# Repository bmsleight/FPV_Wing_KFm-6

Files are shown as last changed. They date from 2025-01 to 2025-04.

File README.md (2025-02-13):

# FPV_Wing_KFm-6

Simple FPV wing model based upon simply cut foam sheets and simple 3d parts

## Basic Materials

The naked model is less than £9. Wingspan 594mm (or 705mm including body).

Aim to have construction to be as simple as possible. So based all dimensions upon A4, 3mm deep foam board. Combined with some 3d printed parts.

Key: Yellow: foam board, Green: Printed parts

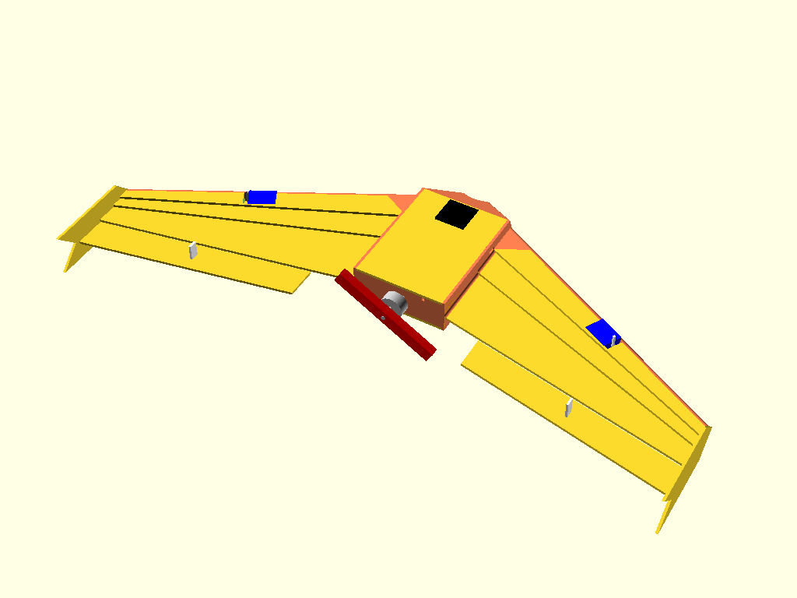
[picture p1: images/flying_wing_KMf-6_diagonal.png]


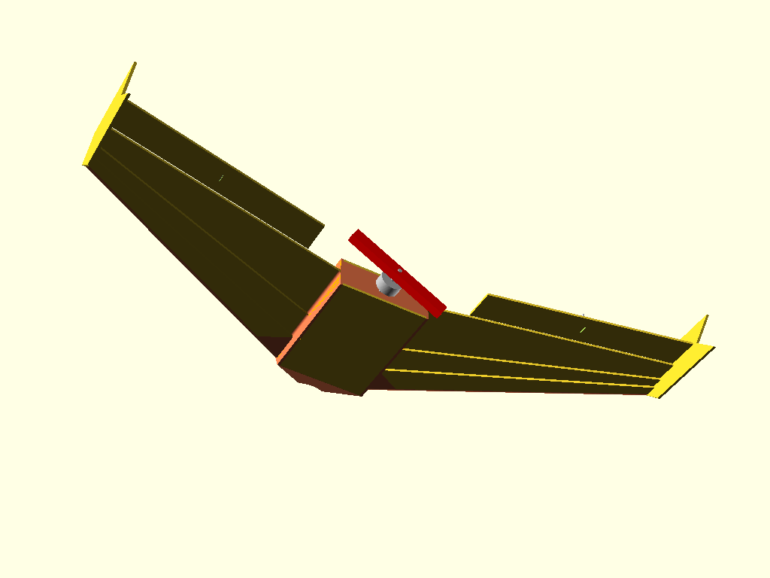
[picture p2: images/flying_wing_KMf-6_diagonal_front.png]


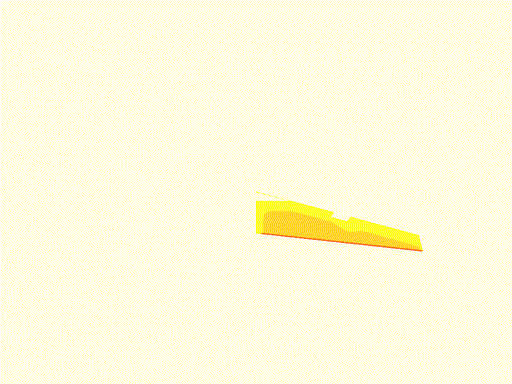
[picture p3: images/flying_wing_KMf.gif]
Model rotated


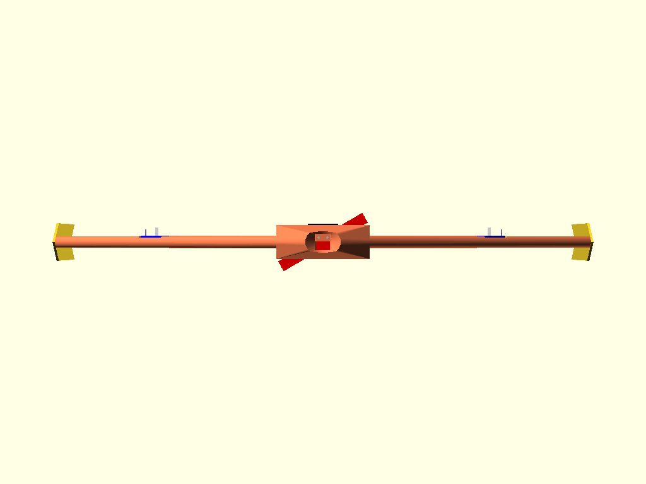
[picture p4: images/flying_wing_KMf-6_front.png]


[Center of Gravity at ~76mm back](http://rcwingcog.a0001.net/?i=1)

## FPV

Total cost, including motors, flight controller, analogue camera, battery, GPS is  £121.63 I was aiming for less than  £100.

## What Makes it Simple

The cuts use the most of the natural dimension of A4 sheets. 

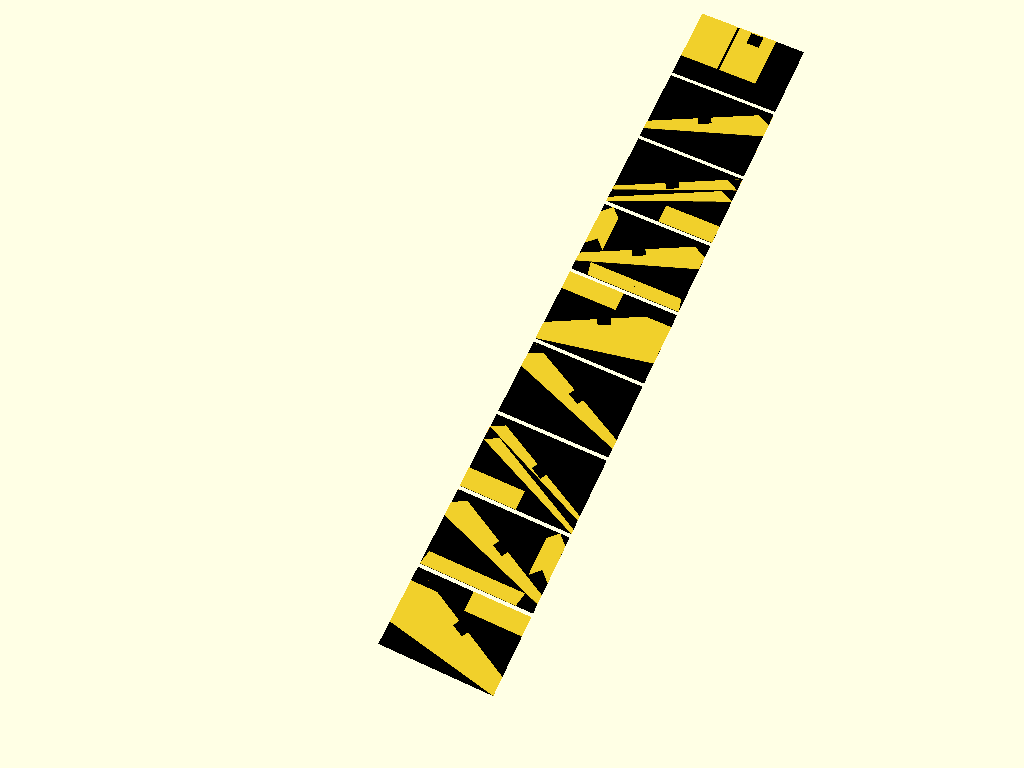
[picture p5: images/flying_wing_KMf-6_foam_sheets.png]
Sheets


Only eight sheets are needed. The model can export directly the SVG file, per page, for printing a template.

Model

The 3d parts can be printed on a standard 200x200 print bed, with only one part requiring supports. The seven individual parts in the [stl directory](https://github.com/bmsleight/FPV_Wing_KFm-6/tree/main/stl)

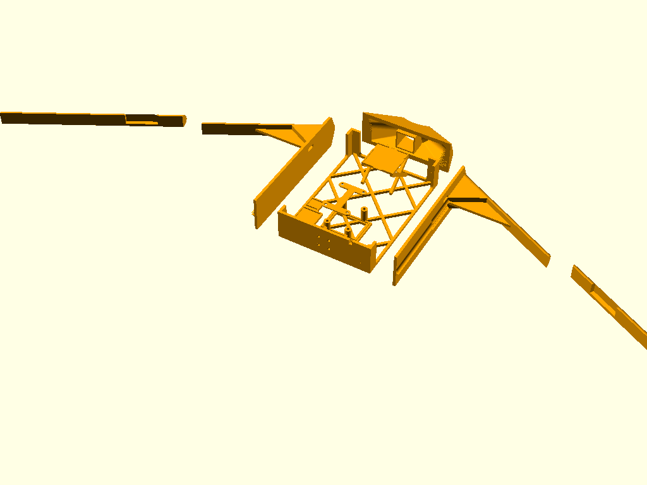
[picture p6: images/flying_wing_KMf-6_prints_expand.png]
https://github.com/bmsleight/FPV_Wing_KFm-6/tree/main/stl Prints Expanded


Model expanded rotated

## Model 

From within OpenSCAD.

Amend display variable to 1 - display model, 2 - print all the printed parts as a print bead, 3 - All the foam parts, 4 - All foam parts as SVGs, 5 - One page SVG file. 

```
display = 1;

module display(display=display)
{
    if(display==1)
    {
        display_model(foam=true, printed_part=true);
    }
    if(display==2)
    {
        print_all();
    }
    if(display==3)
    {
        print_foam_all(outline=true);
    }
    if(display==4)
    {
        projection() print_foam_all(outline=false);
    }
    if(display==5)
    {
        projection() print_foam(page=2, outline=false);
    }
}

display();
```

## Will it Fly ?

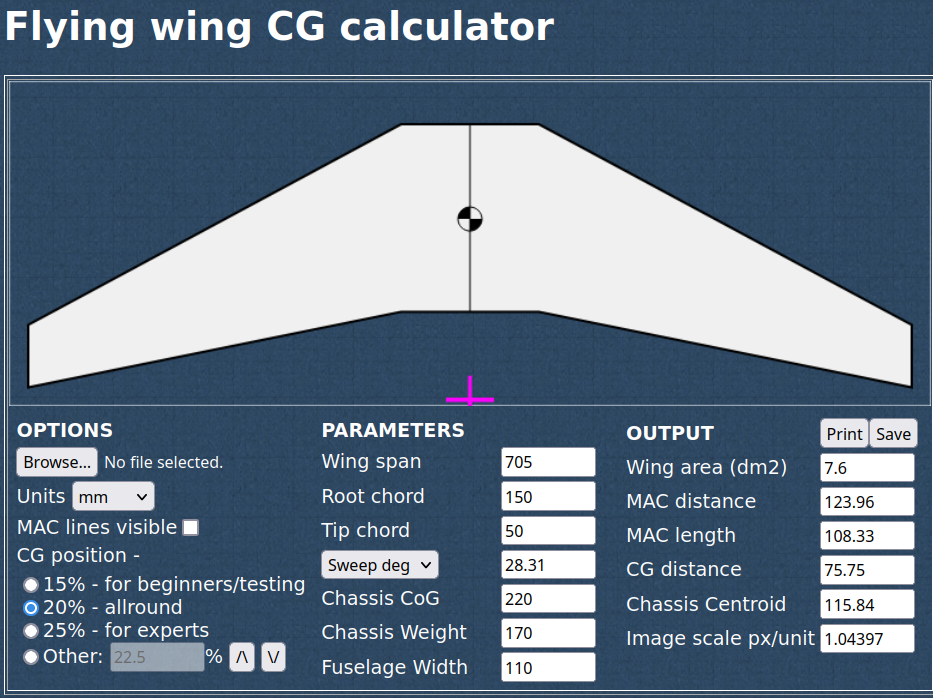
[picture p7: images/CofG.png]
C of G


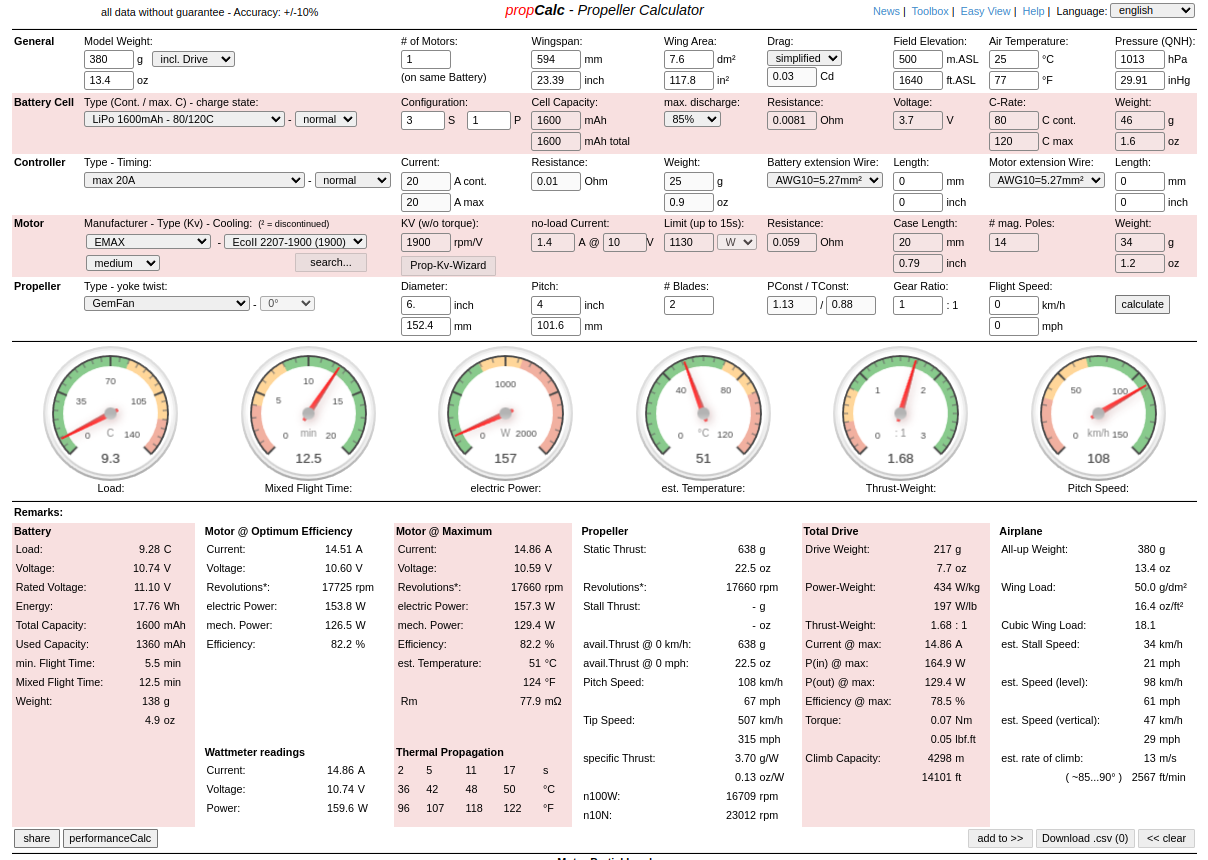
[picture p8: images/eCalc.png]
eCalc


## Parts 

* Printed parts single shell, 15% infill
* Foam board 3mm A4
* Total for naked wing, including glue: 162 grammes 
* ESC 40g  https://www.unmannedtechshop.co.uk/product/dys-20a-2-4s-brushless-esc-with-5v-2a-bec-for-rc-fixed-wing-aircraft/
* Motor 32g https://www.unmannedtechshop.co.uk/product/emax-eco-ii-series-2207-motor/
* Battery 70g, 4S 650mah
 Props https://www.unmannedtechshop.co.uk/product/hqprop-t5-1x2-5x3-grey-propeller-2cw2ccw/
* camera VTX  https://www.aliexpress.com/item/1005008234258917.html?spm=a2g0o.cart.0.0.5ac538dalBiVNT&mp=1 and generic Camera 
* Flight controller (5.6g) https://www.hobbyrc.co.uk/speedybee-f405-wing-mini-flight-controller
* https://www.unmannedtechshop.co.uk/product/tbs-m10-gps-glonass-module/
* servos
* Servo horns https://www.amazon.co.uk/gp/product/B08MDXD3C1/

## Photos

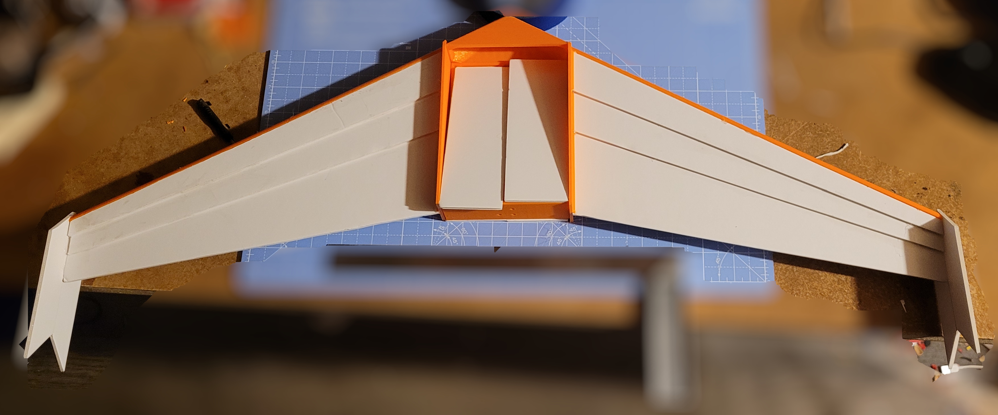
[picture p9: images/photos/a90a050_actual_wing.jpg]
Build naked model


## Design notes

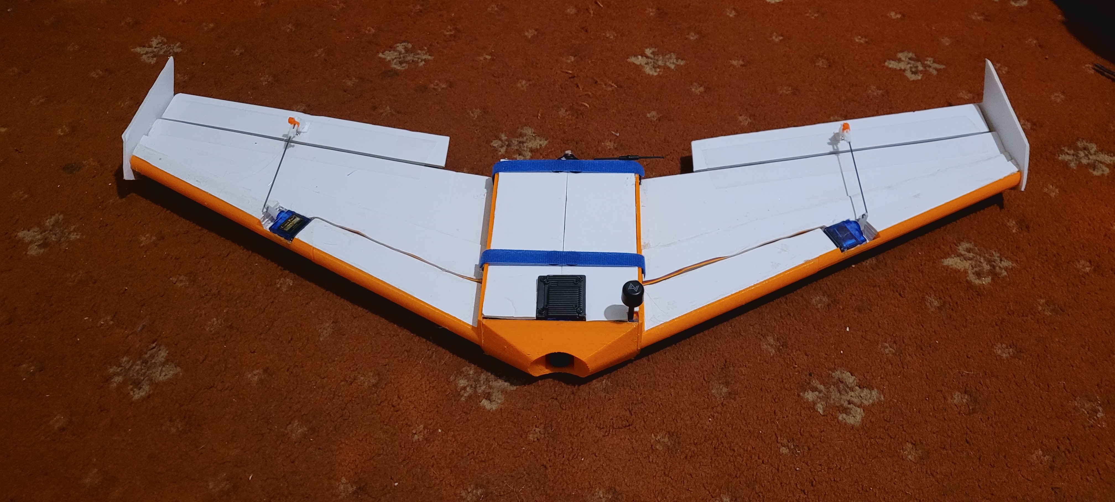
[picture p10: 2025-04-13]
images/photos/aa8055b_actual_wing.jpg

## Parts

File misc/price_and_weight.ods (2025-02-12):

 |  |  |  | £239 | 379.1 g
Frame – foam and prints | 1 | £9 | 161.0 g | £9 | 161.0 g
Batteries – (already had) | 1 | £16 | 100.0 g | £16 | 100.0 g
VTX | 1 | £159 | 22.6 g | £159 | 22.6 g
ESC | 1 | £8 | 40.0 g | £8 | 40.0 g
Motor | 1 | £13 | 31.5 g | £13 | 31.5 g
FC | 1 | £30 | 5.6 g | £30 | 5.6 g
Servo | 2 | £2 | 9.2 g | £4 | 18.4 g

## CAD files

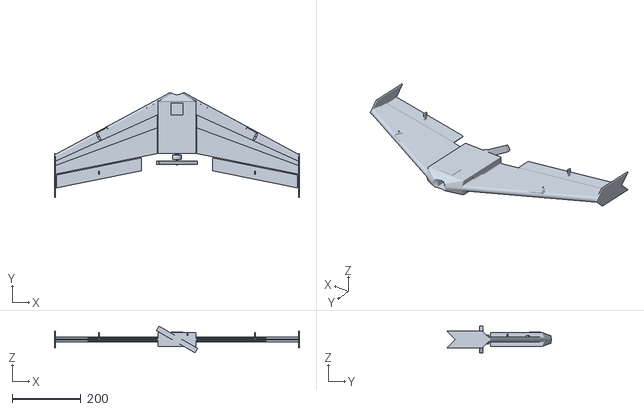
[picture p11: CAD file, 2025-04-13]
stl/flying_wing_KMf-6_full_model.stl
711.0 x 304.0 x 77.7

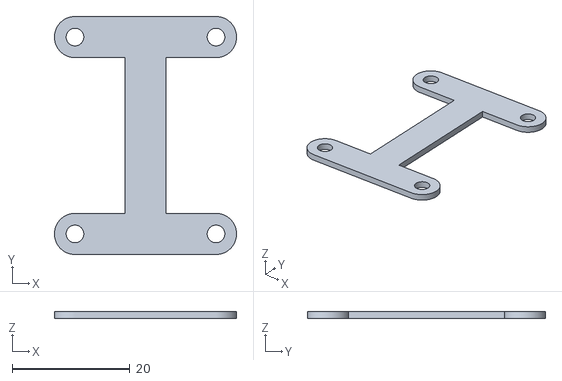
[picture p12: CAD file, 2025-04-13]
stl/flying_wing_KMf-6_printed_part_fc_lid.stl
31.0 x 40.5 x 1.25

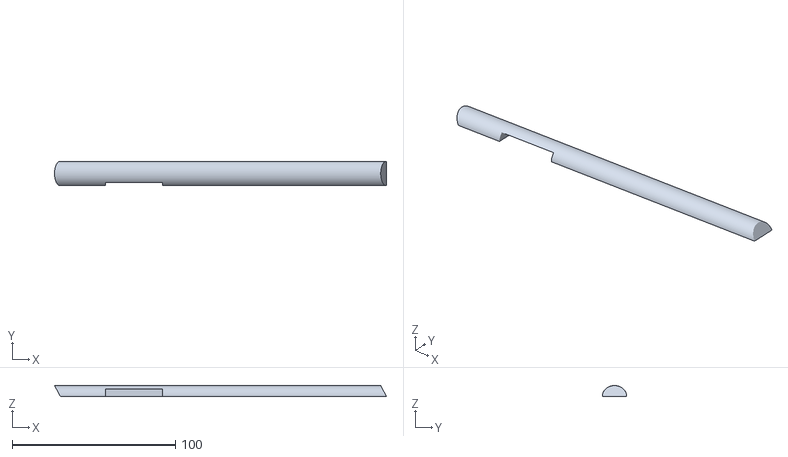
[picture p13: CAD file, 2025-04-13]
stl/flying_wing_KMf-6_printed_part_leading_edge_half.stl
203.5 x 15.0 x 6.71

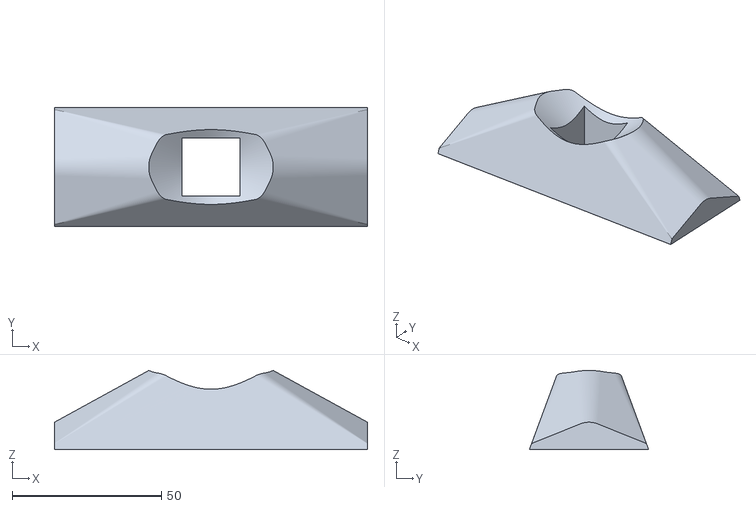
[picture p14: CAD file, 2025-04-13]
stl/flying_wing_KMf-6_printed_part_cockpit_front.stl
105.0 x 40.0 x 26.5

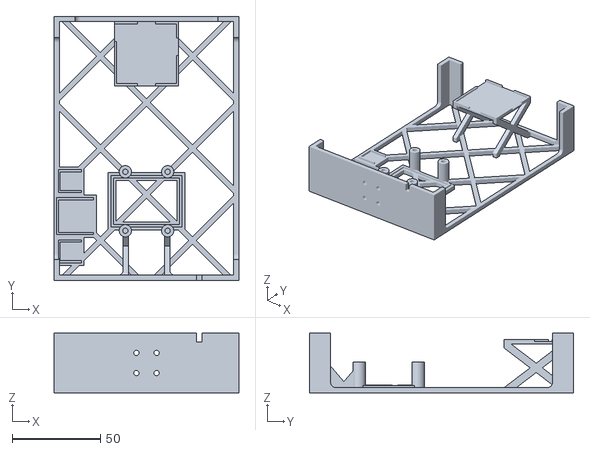
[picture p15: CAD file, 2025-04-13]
stl/flying_wing_KMf-6_printed_part_cockpit.stl
104.8 x 149.9 x 34.0

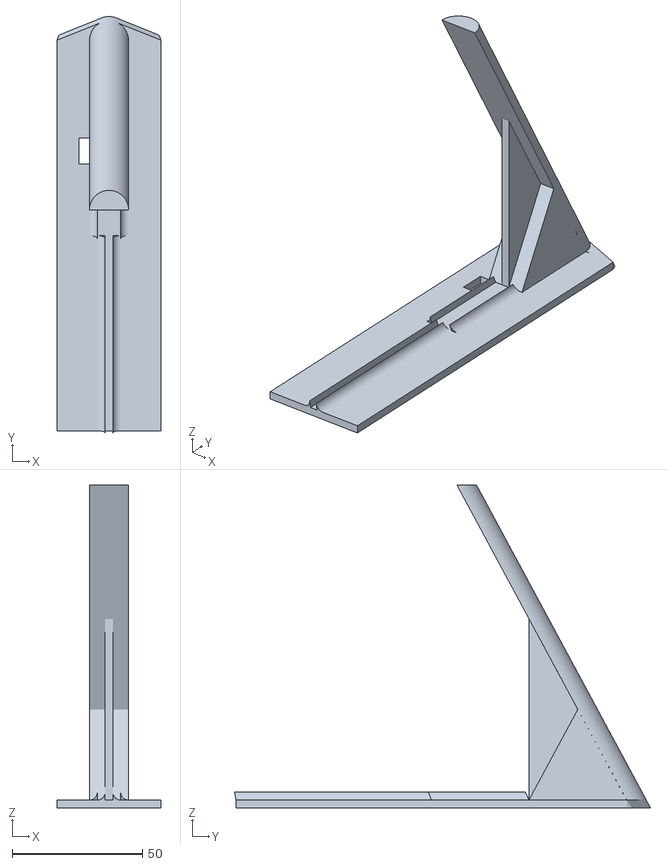
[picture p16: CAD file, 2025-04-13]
stl/flying_wing_KMf-6_printed_part_side_panel.stl
40.0 x 159.8 x 123.9

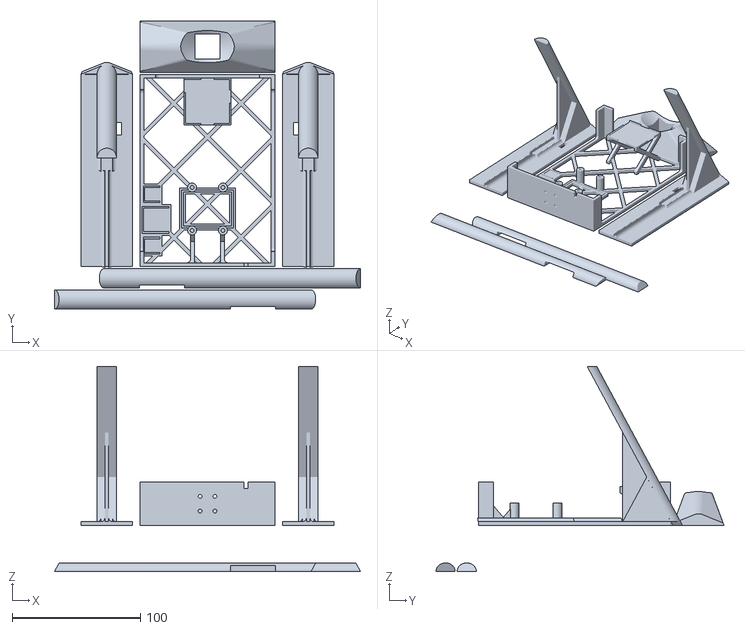
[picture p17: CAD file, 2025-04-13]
stl/flying_wing_KMf-6_printed_parts.stl
238.4 x 224.5 x 159.7

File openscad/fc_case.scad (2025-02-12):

$fn=60;

module pillar(od=7,id=3,ox, oy, oz)
{
    translate([ox/2,oy+od/2,0]) difference()
    {
        cylinder(h=oz,d=od,center=true);
        translate([0,0,oz]) cylinder(h=oz*2,d=id,center=true);
    }
}

module pillars(od=7, id=3, ox, oy, oz)
{
    pillar(od=od,id=id,ox=ox+od, oy=oy, oz=oz);
    mirror([0,1,0]) pillar(od=od,id=id,ox=ox+od, oy=oy, oz=oz);
    mirror([1,0,0]) pillar(od=od,id=id,ox=ox+od, oy=oy, oz=oz);
    mirror([1,0,0]) mirror([0,1,0])  pillar(od=od,id=id,ox=ox+od, oy=oy, oz=oz);
}

module fc_case_top(od, id,t,ox,oy,oz)
{
    difference()
    {
        union()
        {
            hull()
            {
                translate([ox/2+od/2,oy+od/2,0]) cylinder(h=t,d=od,center=true);
                translate([-(ox/2+od/2),oy+od/2,0]) cylinder(h=t,d=od,center=true);
            }
            hull()
            {
                translate([ox/2+od/2,-(oy+od/2),0]) cylinder(h=t,d=od,center=true);
                translate([-(ox/2+od/2),-(oy+od/2),0]) cylinder(h=t,d=od,center=true);
            }
            hull()
            {
                translate([0,(oy+od/2),0]) cylinder(h=t,d=od,center=true);
                translate([0,-(oy+od/2),0]) cylinder(h=t,d=od,center=true);
            }
        }
        translate([ox/2+od/2,oy+od/2,0])  cylinder(h=oz*2,d=id,center=true);
        mirror([0,1,0]) translate([ox/2+od/2,oy+od/2,0])  cylinder(h=oz*2,d=id,center=true);
        mirror([1,0,0]) translate([ox/2+od/2,oy+od/2,0])  cylinder(h=oz*2,d=id,center=true);
        mirror([1,0,0]) mirror([0,1,0]) translate([ox/2+od/2,oy+od/2,0])  cylinder(h=oz*2,d=id,center=true);

    }
}


module fc_case(case=true, fc=true)
{
    t=1.25;
    tolerance=0.5;
    fc_x = 37+tolerance;
    fc_y = 26+tolerance;
    fc_z = 14+tolerance;
    foam_height=3;
    gap=17;
    od=7;
    id=3;
    if(case==true)
    {
        translate([0,0,(fc_z+t*2)/2])
        {
            translate([0,0,-fc_z/2]) difference()
            {
                union()
                {
                    cube([fc_x+foam_height,fc_y+foam_height,t*2], center=true);
                    translate([0,0,-t/2]) cube([fc_x+foam_height*2,fc_y+foam_height*2,t*1], center=true);
                }
                cube([fc_x-foam_height,fc_y-foam_height,t*4], center=true);        
                translate([0,0,t]) cube([fc_x,fc_y,t*2], center=true);
            }
            translate([0,0,-t/2]) pillars(od=od,id=id,ox=gap,oy=fc_y/2, oz=fc_z+t);
            translate([0,0,(fc_z+t)/2]) fc_case_top(od=od, id=id, t=t, ox=gap,oy=fc_y/2, oz=fc_z+t);
    
        }
    }
    if(fc==true)
    {
        translate([0,0,(fc_z+t*2)/2]) color("Red") cube([fc_x,fc_y,fc_z], center=true);
    }
}


fc_case();

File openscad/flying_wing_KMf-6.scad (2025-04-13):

 
//$vpr = [45,0,30];
//$vpt = [0,-150,0];
//$vpd = 1200;

// http://fwcg.3dzone.dk/
// https://www.flitetest.com/articles/kfm-6-flying-wing


// Printed parts 71.75 g single shell, 5% infill
// Foam 123g = 41g per sheet assume 3 sheets (maybe less than 2)
// ESC 40g  https://www.unmannedtechshop.co.uk/product/dys-20a-2-4s-brushless-esc-with-5v-2a-bec-for-rc-fixed-wing-aircraft/
// Motor 32g https://www.unmannedtechshop.co.uk/product/emax-eco-ii-series-2207-motor/
// Battery 70g
// Props https://www.unmannedtechshop.co.uk/product/hqprop-t5-1x2-5x3-grey-propeller-2cw2ccw/
// 312g 
// Add for camera
//  camera VTX  https://www.aliexpress.com/item/1005008234258917.html?spm=a2g0o.cart.0.0.5ac538dalBiVNT&mp=1 and generic Camera 
// Add for flight controller (5.6g) https://www.hobbyrc.co.uk/speedybee-f405-wing-mini-flight-controller
// GPS https://www.unmannedtechshop.co.uk/product/tbs-m10-gps-glonass-module/
// Add for servos


// Used 350g for calcs


// Costs 
// Printed parts: £1.72
// Foam sheets:  £6.99 for 10 sheets
// ESC: £8.49
// Motor: £12.99
// Battery: £14.50
// Props: £2.37
// Camera: 
// Flight Controller: £29.80
// Postage £5.00
// Micro Servo: £1.00
// GPS £14.90
// Wiring and other consumables
// £121.63 1.72+6.99+8.49+12.99+14.50+2.35+13.99+2.80+6.10+29.80+6.00+1.0+14.90


display = 5;
display_page = 9;
expand=false;
accessories = true;
vtx=true;
fc=true;
elrs=true;
elrs_ff=true;
gps=true;
foam=true;
printed=true;
display_part = "side_panel"; //"cockpit" "cockpit_front"  "leading_edge_half" "leading_edge_half_mirror" "side_panel" "side_panel_mirror" "fc_lid")


module display(display=display)
{
    if(display==1)
    {
        display_model(foam=foam, printed_part=printed);
        if(accessories==true)
        {
            motor_and_prop();
            servo();
            mirror([1,0,0]) servo();
            servo_horn();
            mirror([1,0,0]) servo_horn();
            vtx_case(case=false, vtx_unit=true);
            just_fc();
        }
    }
    if(display==2)
    {
        print_all_new();
    }
    if(display==3)
    {
        print_foam_all(outline=true);
    }
    if(display==4)
    {
        projection() print_foam_all(outline=false);
    }
    if(display==5)
    {
        projection() print_foam(page=display_page, outline=false);
    }
    if (display==6)
    {
        echo(display_part);
        if(display_part=="cockpit_front")
        {
            print_part_cut(cut=1);
        }
        if(display_part=="side_panel")
        {
            print_part_cut(cut=2);
        }
        if(display_part=="side_panel_mirror")
        {
            print_part_cut(cut=5);
        }
        if(display_part=="leading_edge_half")
        {
            print_part_cut(cut=3);
        }
        if(display_part=="leading_edge_half_mirror")
        {
            print_part_cut(cut=6);
        }
        if(display_part=="cockpit")
        {
            print_part_cut(cut=4);
        }
        if(display_part=="fc_lid")
        {
            print_part_cut(cut=7);
        }
    }
    if(display==7)
    {
        expand_prints();
    }
}

display();



// The OpenSCAD Variables

$fn=120;


a4_h = 297;
a4_w = 210;
foam_height = 3;

wing_span = a4_h*2;
root_cord = 150;
tip_cord = 50;

aileron_offset = 50;
aileron_offset_w = 37.5;

// Make the top of bottom of cockpit eqaul 1/2 width of a4 - easier to square-up
cockpit_x = a4_w/2+foam_height*2;
cockpit_y = root_cord;
cockpit_z = 40;
cockpit_thickness = foam_height;
camera = 19.5;
cockpit_window_diameter = camera+cockpit_thickness;
cw_b=cockpit_window_diameter*3;

cockpit_motor_spacing = 11.5;
cockpit_motor_spacing_hole = 3;
cockpit_motor_spacing_hole_wire_x = 3;
cockpit_motor_spacing_hole_wire_y = 10;
cockpit_motor_spacing_hole_wire_offset = 30;
cockpit_motor_stuct_y = 22;
cockpit_motor_stuct_y_gap=17+7/2;

sweep_d = atan((a4_w-tip_cord)/(a4_h));
sweep_d_l1 = atan((a4_w-tip_cord+tip_cord*0.25-root_cord*0.25)/(a4_h));
sweep_d_l2 = atan((a4_w-tip_cord+tip_cord*0.5-root_cord*0.5)/(a4_h));
sweep_d_l3 = atan((a4_w-tip_cord+tip_cord-root_cord)/(a4_h));

size_of_printer=200; // Diagonal 
height_hypo_size_of_printer = size_of_printer * cos(sweep_d);
height_adj_size_of_printer = size_of_printer * sin(90-sweep_d);
height_of_leading_edge_first_section=wing_span/2-height_adj_size_of_printer  ;
// height_of_leading_edge_first_section=(root_cord*0.25)/tan(sweep_d) ;


aileron_d = atan ( (a4_w - root_cord) /  a4_h); 

hinge = 2.5;
aileron_y = tan(aileron_d) * aileron_offset + hinge; 

servo_y = 10;
servo_z = 4;
servo_body_x = 23;
servo_body_y = 34 - 2.5;
servo_body_z = 12.; // actuall 12.4 but we want two foam protected

servo_horn_x =  2.5;
servo_horn_y =  10;
servo_horn_z =  20;
servo_horn_hole_x = 1;
servo_horn_hole_y = servo_horn_y;

servo_hole_x = servo_body_x + 1;
servo_hole_y = servo_body_y + servo_horn_x + 1;
servo_hole_x_offset = foam_height;
servo_hole_y_offset = foam_height;


servo_position_x= (size_of_printer-servo_body_y/2-(foam_height*9)) * cos(sweep_d)+cockpit_x/2; // Not calculated - too hard
servo_position_y= -(size_of_printer+servo_body_x/2-(foam_height*9)) * sin(sweep_d); // Not calculated - too hard
servo_position_rotate =  sweep_d+90;

fc_y_offset=-30;

elrs_x=10;
elrs_x_offset = 4;
elrs_y_offset = 5;

gps_x=18;
gps_x_offset = 3;
gps_y_offset = 29;

elrs_ff_x=elrs_x;
elrs_ff_x_offset = elrs_x_offset;
elrs_ff_y_offset = 45;

// Spin prop during animation
prop_a = 30;


echo("wing_span: ", wing_span);
echo("wing_span inc body: ", wing_span+cockpit_x);
echo("Sweep degrees: ", sweep_d);
echo(height_hypo_size_of_printer, $vpr, $vpd  );

// The OpenSCAD modules 

module A4()
{
    square(size = [a4_w, a4_h], center = false);
}

module profile_leading_edge()
{
    difference()
    {
        rotate([0,90,0]) cylinder(h=0.1, r = foam_height*2.5, center = true);
       translate([0,-foam_height*5/2,0]) cube(foam_height*5, center=true);
    }
}

module leading_edge_chamfer()
{
        difference()
    {
        hull()
        {
            translate([-foam_height/2,0,foam_height*6/2]) side_slot(0.5, start_angle=sweep_d, end_angle=sweep_d);    
        profile_leading_edge();
        }
        translate([-foam_height/2,0,foam_height*6/2])  difference()
        {
            translate([foam_height,0,0]) cube([foam_height,10,foam_height], center=true);
            side_slot(10+foam_height, start_angle=sweep_d, end_angle=sweep_d);
        }
    }
}

module leading_edge()
{
    color("green") hull()
    {
        translate([0.1,0,0])  profile_leading_edge();
        translate([wing_span/2-0.1,-(a4_w-tip_cord),0]) profile_leading_edge();
    }
    scale([1,1,1.002])   translate([0,foam_height,0])
    translate([0,-tan(sweep_d)*height_of_leading_edge_first_section,0])
*    translate([height_of_leading_edge_first_section/2,0,0]) cube([height_of_leading_edge_first_section, foam_height*2, foam_height*3+0.01], center=true);

//    translate([0,foam_height,0])
//    translate([0,-tan(sweep_d)*height_of_leading_edge_first_section,0])
//    translate([height_of_leading_edge_first_section/2,0,0]) 
    scale([1,1,1.002])  intersection()
    {
        translate([0,0,-foam_height*2.5]) linear_extrude(height=foam_height*5) polygon(points=[[0,0],[0,-(a4_w-tip_cord)],[wing_span/2,-(a4_w-tip_cord)]]);
        translate([0,-root_cord*0.25,-foam_height*2.5]) rotate([0,0,sweep_d]) cube([height_of_leading_edge_first_section, wing_span, foam_height*5+0.01], center=false);
    }

    scale([1,1,1.002])  intersection()
    {
        translate([0,0,-foam_height*2.5]) linear_extrude(height=foam_height*5) polygon(points=[[0,0],[0,-(a4_w-tip_cord)],[wing_span/2,-(a4_w-tip_cord)]]);
        translate([0,-root_cord*0.25,-foam_height*0.5]) rotate([0,0,0]) cube([root_cord*0.25/tan(sweep_d), wing_span, foam_height*1+0.01], center=false);
    }

    
*    leading_edge_chamfer();
*    mirror([0,0,1]) leading_edge_chamfer();

}


module wing_part_not_cut(cord_percentage = 1)
{
    point_1_y = tan(sweep_d) * wing_span/2;
    linear_extrude(foam_height, center = true) polygon(points=[[0,0],[wing_span/2,-point_1_y], [wing_span/2,-point_1_y], [wing_span/2,-point_1_y-tip_cord*cord_percentage], [0,-root_cord*cord_percentage]]);
}


module wing_part_cut_by_support(cord_percentage = 1)
{
    if(cord_percentage == 1)
    {
        scale([1,1,2]) translate([-foam_height,-root_cord/2,0])  rotate([0,90,0]) print_part_cut(cut=2);
    }
    if(cord_percentage != 1)
    {
        translate([0,0,foam_height*2]) scale([1,1,2]) translate([-foam_height,-root_cord/2,0])  rotate([0,90,0]) print_part_cut(cut=2);
    }
}
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

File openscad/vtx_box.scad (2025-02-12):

$fn=60;




foam_height = 3;

module strut(sx1,sy1,sx2,sy2,sz, unit)
{
    hull()
    {
        translate([sx1,sy1,unit/2]) cube(unit,center=true);
        translate([sx2,sy2,sz]) cube(unit,center=true);
    }
    
}

module struts(sx1,sy1,sx2,sy2,sz, unit)
{
    strut(sx1,sy1,sx2,sy2,sz, unit);
    mirror([1,0,0]) strut(sx1,sy1,sx2,sy2,sz, unit);
    mirror([0,1,0]) strut(sx1,sy1,sx2,sy2,sz, unit);
    mirror([1,0,0]) mirror([0,1,0]) strut(sx1,sy1,sx2,sy2,sz, unit);
    strut(sx1,sy1,-sx1,sy1,unit/2, unit);
    mirror([0,1,0])  strut(sx1,sy1,-sx1,sy1,unit/2, unit);
}

module vtx_case()
{
    inside=34;
    t=1.25;
//    z_i=5+5-5;
    z_i=t*2;

    cx=inside+t*2;
    cy=inside+t*2;
    cz=z_i;
    vtx_height = 40;

    translate([0,0,vtx_height-cz/2]) difference()
    {
        cube([cx,cy,cz],center=true);   
        translate([0,0,t]) rotate([0,0,0]) union()
        {
            cube([inside,inside,z_i],center=true);
            // usb 
            translate([0,inside/2,0]) cube([10,inside,z_i], center=true);
            // cam
            translate([inside/2,inside/2-10/2-8,0]) cube([inside,10,z_i], center=true);
            // cables FC 
            translate([0,-inside/2,0]) cube([10,inside,z_i], center=true);
            // Antenna
            translate([-inside/2,inside/2-10/2,0]) cube([inside,10,z_i], center=true);
        }
    }
    struts(-cx/2+foam_height/2,-cy/2+foam_height/2,-cx/2+foam_height/2,-(-cy/2+foam_height/2),vtx_height-cz-foam_height/2+t/2, foam_height);
}




vtx_case();

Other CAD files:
stl/flying_wing_KMf-6_printed_part_side_panel_mirror.stl
stl/flying_wing_KMf-6_printed_part_leading_edge_half_mirror.stl

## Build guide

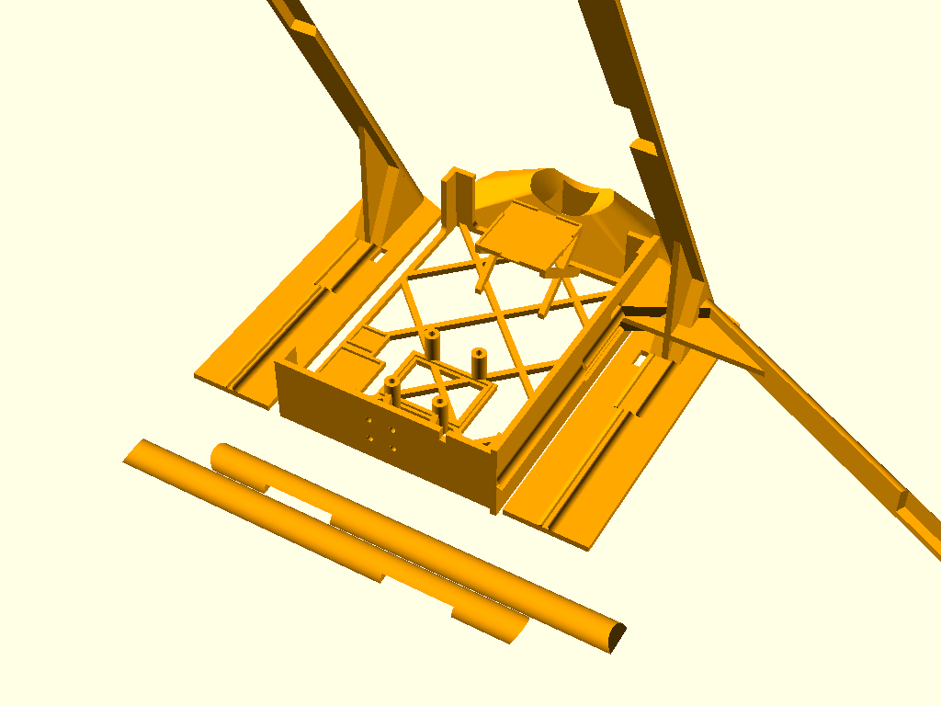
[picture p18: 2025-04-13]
images/flying_wing_KMf-6_prints.png

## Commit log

2025-01-10 Update README.md - remove STL
2025-01-10 Adding Printed Parts stl
    [flying_wing_KMf-6_printed_parts.stl]
2025-01-11 Adding scripts to generate all files
    [flying_wing_KMf-6.scad, flying_wing_KMf-6_full_model_2.stl, flying_wing_KMf-6_printed_parts.stl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]
2025-01-11 Bigger aileron
    [flying_wing_KMf-6.scad]
2025-01-11 Bigger aileron - files updates
    [flying_wing_KMf-6_printed_parts.stl]
2025-01-12 Stronger Cockit - files updates
    [flying_wing_KMf-6.scad, flying_wing_KMf-6_printed_part_cockpit.stl, flying_wing_KMf-6_printed_part_cockpit_front.stl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]
2025-01-12 Motor mounting corrected - files updates
    [flying_wing_KMf-6.scad, flying_wing_KMf-6_printed_part_cockpit.stl, flying_wing_KMf-6_printed_part_cockpit_front.stl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]
2025-01-12 Added two pages - files updates
    [flying_wing_KMf-6.scad, flying_wing_KMf-6_printed_part_cockpit.stl, flying_wing_KMf-6_printed_part_cockpit_front.stl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]
2025-01-14 Mirror, mirror - files updates
    [flying_wing_KMf-6.scad, flying_wing_KMf-6_printed_part_cockpit.stl, flying_wing_KMf-6_printed_part_cockpit_front.stl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]
2025-01-17 Side-panels branch
    [flying_wing_KMf-6.scad, flying_wing_KMf-6_printed_part_cockpit.stl, flying_wing_KMf-6_printed_part_cockpit_front.stl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]
2025-01-17 Side-panels completed
    [flying_wing_KMf-6.scad, flying_wing_KMf-6_full_model.stl, flying_wing_KMf-6_printed_part_cockpit.stl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]
2025-01-17 Tidy files
    [flying_wing_KMf-6_full_model.stl, flying_wing_KMf-6_full_model_2.stl, flying_wing_KMf-6_printed_parts_ascii.stl]
2025-01-18 Correcting bash script for STL export
    [flying_wing_KMf-6.scad, flying_wing_KMf-6_full_model.stl, flying_wing_KMf-6_printed_part_cockpit.stl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]
2025-01-22 Changing front cockpit to indent camera
    [flying_wing_KMf-6.scad, flying_wing_KMf-6_full_model.stl, flying_wing_KMf-6_printed_part_cockpit.stl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]
2025-01-29 Add servo and make that prop spin
    [flying_wing_KMf-6.scad, flying_wing_KMf-6_full_model.stl, flying_wing_KMf-6_printed_part_cockpit.stl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]
2025-02-03 Servo in position and cutting foam - part commit
    [flying_wing_KMf-6.scad, flying_wing_KMf-6_full_model.stl, flying_wing_KMf-6_printed_part_cockpit.stl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]
2025-02-04 Moving servos
    [flying_wing_KMf-6.scad, flying_wing_KMf-6_full_model.stl, flying_wing_KMf-6_printed_part_cockpit.stl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]
2025-02-12 Addign options for VTX and FC
    [fc_case.scad, flying_wing_KMf-6.scad, flying_wing_KMf-6_full_model.stl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]
2025-02-13 tweakign how model are show in readme
    [flying_wing_KMf-6.scad, flying_wing_KMf-6_full_model.stl, flying_wing_KMf-6_printed_part_cockpit.stl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]
2025-04-13 Addign struct to reduce flex
    [flying_wing_KMf-6.scad, flying_wing_KMf-6_full_model.stl, flying_wing_KMf-6_printed_part_cockpit.stl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]
2025-04-13 Addign struct to reduce flex 2
    [flying_wing_KMf-6.scad]
2025-04-13 Addign struct to reduce flex 3
    [flying_wing_KMf-6.scad, flying_wing_KMf-6_full_model.stl, flying_wing_KMf-6_printed_part_cockpit.stl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]
